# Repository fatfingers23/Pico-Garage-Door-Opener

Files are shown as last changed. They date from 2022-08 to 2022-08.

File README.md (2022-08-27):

# Super simple garage door opener using a Pico W

I live in an apartment with a detached garage where the only entrance is through the garage door, and if you forget the remote in the garage, you are locked out. This was my solution for WiFi enabled garage door opener with these conditions and no WiFi within reach of the garage. This sits in my apartment about 200ft from my garage, and still able to trigger it.

My finished product.
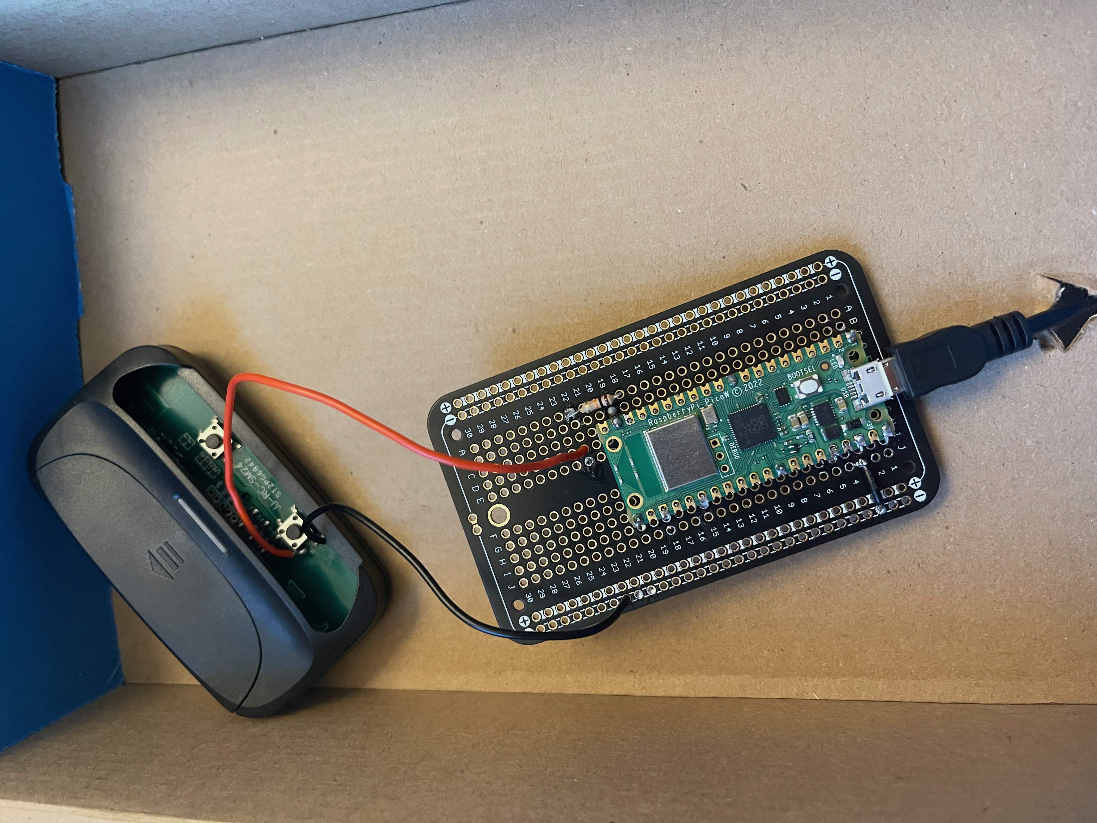
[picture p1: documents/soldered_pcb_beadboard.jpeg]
soldered pcb


# Parts
* $6 [Raspberry Pico W](https://www.canakit.com/raspberry-pi-pico-w.html)
* $13 [Cheap Garage Remote](https://www.amazon.com/dp/B08RSDQKM9?psc=1&ref=ppx_yo2ov_dt_b_product_details)
* Perfectly okay to leave in a breadboard, but I decided to solder to this [PCB](https://www.amazon.com/dp/B07ZYNWJ1S?psc=1&ref=ppx_yo2ov_dt_b_product_details) to make it a bit more permanent. But note you will need headers soldered to the pico to be able to plug a micro USB into the pico. If I had to do it over, I'd use this [PCB](https://shop.pimoroni.com/products/pico-proto-pcb?variant=39795939737683) made for Pico and solder directly to the PCB.
* 1 10k ohm resistor. It may not be needed, but I did not want much voltage going to the garage door opener if not be required.

# Wiring Diagram
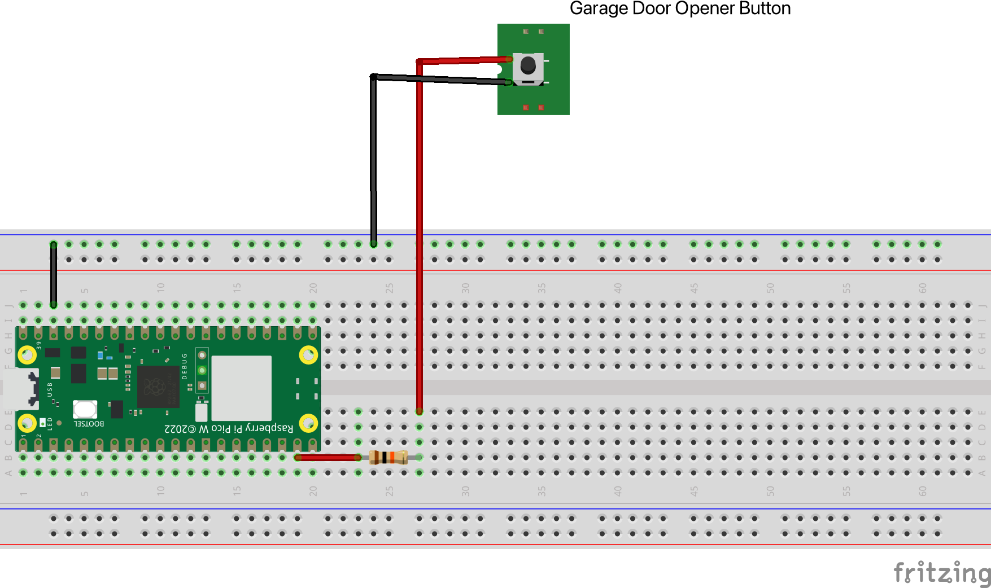
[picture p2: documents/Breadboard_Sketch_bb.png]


# Hardware Setup
* For the garage door remote, you can take it apart by two small Phillips head screws on the back.
* Once open, I'd hold it with the buttons on the bottom facing you. Then you solder your GPIO pin to the top lead left from the button to the PCB. Then solder your ground to the bottom left lead. If you buy a different remote, you can use a piece of wire to connect the two; if it lights up, then that's where it should be wired. You can also use a volt to find what is needed. What I did initially.
* Setup the remote for your garage motor following directions included with the remote. I'd solder the wires in and test that you can trigger a button press before setting up the remote with your garage to cut down on how many times it opens and close
* Wire up as seen in the diagram.

# Software Setup
You will find a [settings.json.example](settings.json.example). This file holds all the settings for this project.
Remove the `.example` so the file becomes `settings.json`, then enter your values.
* ssid - Your WiFi name
* ssid_password - Your WiFi password
* password - A clear-text password is needed to open your garage (100% not the most secure, just a bit of a determent if you are port forwarding to your pico).

1. Download and set up MicroPython. If not already can find out [here](https://www.raspberrypi.com/documentation/microcontrollers/micropython.html).
2. Copy [main.py](main.py) and [settings.json](settings.json) to your Pico. (Can use [rshell](https://github.com/dhylands/rshell#cp) or [Throny](https://www.freva.com/transfer-files-between-computer-and-raspberry-pi-pico/) for this)
3. Using REPL for the pico should print the IP address. Use that and type `http://{pico-ip}/garage/toggle/{password-from-settings}` should see a web page and the pico light flash meaning it toggled GPIO Pin 14 to open the garage door. I set opening this URL to a shortcut on my iPhone to trigger the door.

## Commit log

2022-08-26 Documentation (#1)
    Finishing touches
    [Breadboard_Sketch.fzz]
2022-08-27 Did not realize the prototype picture was 15mbs
